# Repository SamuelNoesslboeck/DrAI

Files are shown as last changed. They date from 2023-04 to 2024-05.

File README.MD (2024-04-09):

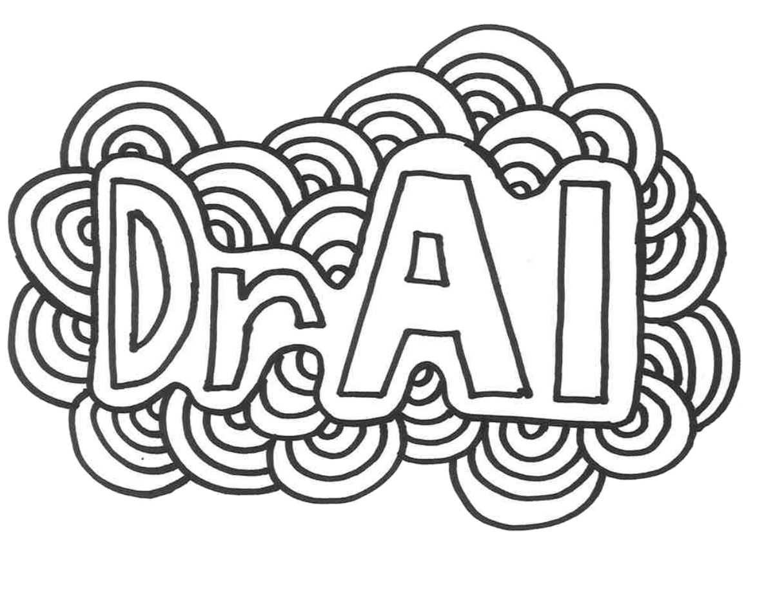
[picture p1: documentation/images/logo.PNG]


# DrAI

Diploma project estimated in January 2023 in collaboration with [**Ars Electronica Center Linz**](https://ars.electronica.art/) and the [higher secondary vocational college Neufelden](https://htl-neufelden.at).

## Thesis, repo folders and further reading

The thesis is available for everyone to read [here](/documentation/Projektbeschreibung.pdf).

All the important folders of this repository contains a *README.md*-file with basic information about the folder itself and important subfolders. As does this folder:

- [code](code/): Code projects for robot control, AI and more 
- [construction](construction/): Parts and drawings for the robot, electronics and other builds
- [documentation](documentation/): Images, graphics, the documentation and the written diploma thesis
- [drake_printer_files](https://github.com/sn-printer-files/drake_printer_files): A subrepository for managing all the *GCODE*-files for the 3D-printed parts of the project
- [electronics](electronics/): Contains all the schematics for the electronics of the project
- [sketches](sketches/): Sketches and basic concept art created for this project, indexed and documentated
- [standard](standard/): Folder with additional standard-parts, will be removed in the future

## Overview

- [DrAI](#drai)
  - [Thesis, repo folders and further reading](#thesis-repo-folders-and-further-reading)
  - [Overview](#overview)
  - [Summary](#summary)
    - [Goal](#goal)
    - [Task](#task)
      - [Software](#software)
      - [Robot](#robot)
  - [Construction](#construction)
  - [AI](#ai)
  - [Electronics](#electronics)

## Summary

### Goal

The goal of this project is to demonstrate the capabilities of AI in completing "creative" tasks in collaboration with humans.

### Task

The final result will be an interactive robot equipped with an AI trained to interpret pre-drawn sketches from the user and complete them with its own "creativity".  
To start this interaction, the user will have to draw some sketch onto a piece of paper, which then is transported into the robot. Once the sheet is in the robot, its goal is to unwrap its "creative" potentials by drawing additional lines onto the paper of the user. The opportunities are limitless here, the AI can for example create a forest next to a cottage the user has drawn onto the sheet, or a beach to some water and so on.

The project can be split up into the two main parts AI (or in general software) and the robot (hardware).

#### Software

First the software has to locate the sheet with a digital camera mounted to the tool and take a picture of it. Then all the lines drawn by the user are detected and interpreted. The fewer lines made by the user, the more "creative" the AI can be. All the merged lines generated are then transfered to the robot.

The software first puts the picture taken into a vision-transformer that creates a description for it, which is then used by a Stable Diffusion Algorithm to generate a colored RGB-image. Out of this images, another algorithm extracts the edges and merges them with the original image.

The robot os is made in rust and allows basic movements required to draw the lines. (See [sybot](https://github.com/SamuelNoesslboeck/sybot))

#### Robot

The robot has to, as already mentioned, be able to draw lines on an A5 sheet of paper. To do this, it will be equipped with a printer tool and three dynamic (X, Y, Z) axes that it can move to any exact position in range it desires.

The user interface should be as simple as possible, not more then two buttons even.

## [Construction](./construction/)

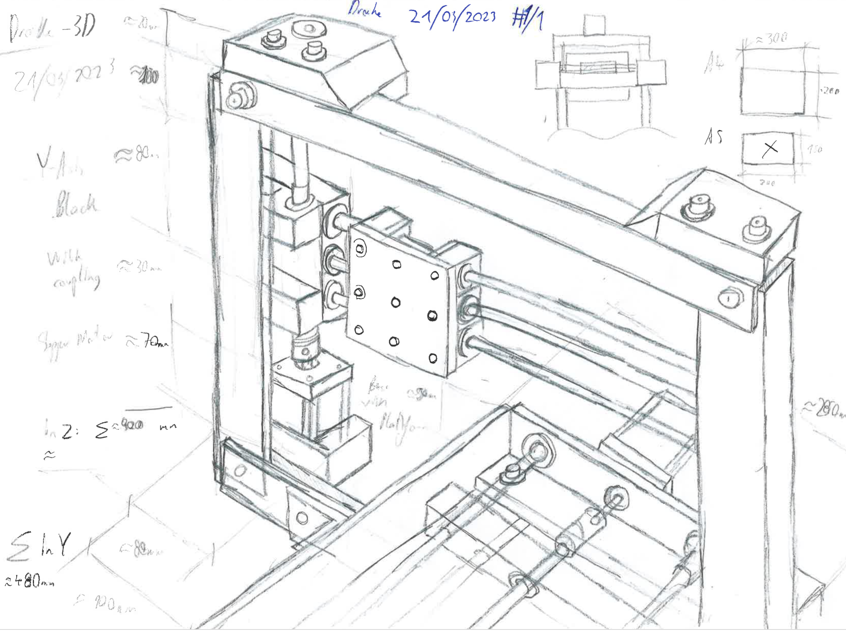
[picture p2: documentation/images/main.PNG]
Old sketch


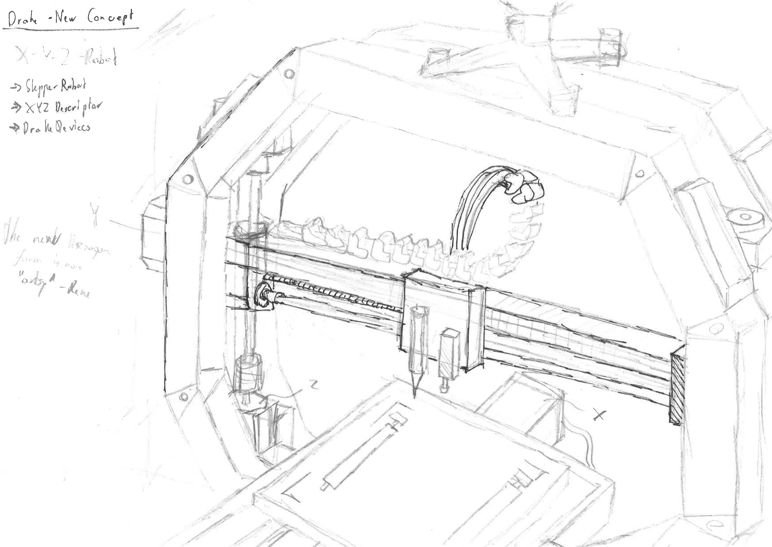
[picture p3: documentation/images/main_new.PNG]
New sketch


The construction is similar to the one of a 3D-Printer including three stepper-motor controlled linear axis, a BLTouch and endswitches to measure home position and more. A welded aluminum frame is the basis for the robot and with the vast majority of the other parts being 3D-printed, the manufactoring process turned out to be quite simple.

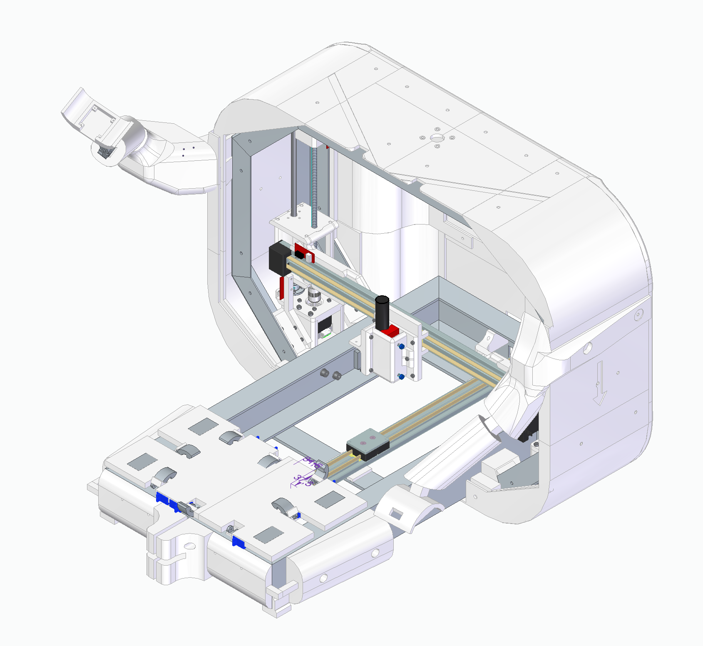
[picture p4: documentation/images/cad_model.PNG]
CAD


## AI

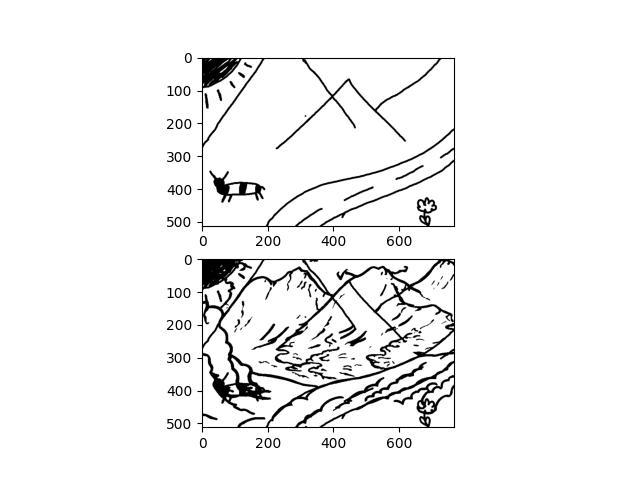
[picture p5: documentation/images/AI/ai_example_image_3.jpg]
AI Example 1


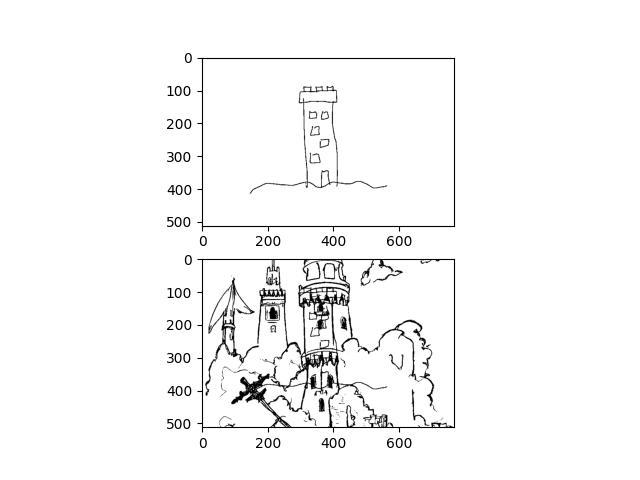
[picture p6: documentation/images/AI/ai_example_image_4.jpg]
AI Example 2


## Electronics

The electronics consist of the main robot driver and the additional control systems, with the main driver being equipped with multiple high-power stepper motor controllers, as we do not want the user to wait more than five minutes for their picture.

- [Driver README](./electronics/drake_electronics/README.md)

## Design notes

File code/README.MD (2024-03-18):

# Code

Contains all the code projects for robot control, AI and more

## Relevant subfolders

- [ai_pipeline](ai_pipeline/): Everything related to the AI-Pipeline
- [drake_ctrl](drake_ctrl/): The control software of the robot
- [network](network/): Helper scripts for the network connection
- [scripts](scripts/): Scripts and batch files required for setup, updating and maintaining
- [syact](https://github.com/SamuelNoesslboeck/syact): The *syact* library for stepper motor control and management of devices
- [sybot](https://github.com/SamuelNoesslboeck/sybot): The *sybot* library for robot controls
- [sylo](https://github.com/SamuelNoesslboeck/sylo): The *sylo* library for peripheral controls

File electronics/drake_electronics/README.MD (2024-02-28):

# drake electronics

## Summary

The main electronics of the drake robot, including four stepper controllers, a high amount of measurement devices, sensors and up to two cameras.

## Stepper controllers

Supplied with a high voltage and current of 24-36V and ~2A the motors need a powerful controller that can manage high step frequencies as microstepping is used. Assuming a step count of 200 with a microstepping of 16, the frequency required to create a speed of 10rev/s evaluates to 32kHz, which is about the maximum for stepper motor controllers of this size.

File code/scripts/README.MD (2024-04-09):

# Scripts

Scripts and batch files required for setup, updating and maintaining

## General scripts

General purpose scripts

- [env](env.sh)(.sh/.bat): Sets all the environment variables required for other scripts, executing in advance will not be required!
- [setup](setup.sh)(.sh/.bat): Setup script that should be called after installing to ensure functionality
- [update](update.sh)(.sh/.bat): Updates all repos if there are any available

## [Start scripts](./start/)

Scripts for starting up the main processes for a specific device (e.g. drai-camera).

- [camera.sh](start/camera.sh)
- [ctrl.sh](start/ctrl.sh)
- [server.sh](start/server.sh)
  
## Test scripts

Scripts for testing the functionallity of electronics and connections.

- []

### Standard test routine

To run the full [standard test routine](./testing.sh) run:

```sh
# Go to the project root directory, default being:
cd ~/DrAI

sh "code/scripts/testing.sh"
```

## Calibration scripts

Scripts for the calibration of the robot.

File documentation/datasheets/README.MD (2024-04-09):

# Datasheets

A list of datasheets for the components used in the project:

1. [PCA9685 Board](./1_pca9685_board.pdf): The servo driver board used in the drawing table
2. [PCA9685 Chip](./2_pca9685_chip.pdf): The servo driver chip

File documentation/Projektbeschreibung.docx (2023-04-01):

Projektbeschreibung

Ziel:

Ziel des Projektes ist es, die kreativen Möglichkeiten einer Künstlichen Intelligenz darzustellen.

Aufgabe:

Aufgabe des Projekts ist es, einen interaktiven Roboter mit einer künstlichen Intelligenz zu kombinieren. Die Aufgabe sollte hierbei sein, eine grobe vorgefertigte Skizze, fertig zu zeichnen im Sketch-Zeichen-Stil.

Hierfür zeichnet der Besucher zum Beispiel ein Haus aus einem Viereck und einem Dreieck auf ein A5 Papier. Dieses Blatt Papier wird nun auf eine Fläche des Roboters gelegt. Bei der Konstruktion des Roboters ist der dümmste anzunehmende Besucher, daB anzunehmen. Sobald das Blatt Papier am Roboter liegt, ist seine Aufgabe nun sich kreativ auszuleben. Er könnte zum Beispiel weitere Häuserskizzen zeichnen, um ein Dorf zu erstellen oder er könnte einen Wald neben dem Haus anfertigen. Die Möglichkeiten sind hierbei schier grenzenlos.

Dieses Projekt lässt sich in zwei Teile unterteilen. In den Roboter, der die Zeichnung auf das Blatt Papier bringt und die Software, die das anfänglich gezeichnete interpretiert und fertigstellt.

Software:

Ziel der Software ist es das Blatt Papier zu lokalisieren und eine digitale Version davon zu erstellen. Im nächsten Schritt werden die gezeichneten Linien erkannt. Aus den gesammelten Daten wird das Bild interpretiert und erweitert. Im letzten Schritt werden die zu zeichnenden Kanten an den Roboter weitergegeben. Um dies zu realisieren wird eine Kamera verwendet, die von der Vogelperspektive aus auf das Blatt Papier fotografiert. Diese digitale Version wird in einen V14-Transformer gegeben, dieser erzeugt eine Beschreibung der anfänglich gezeichneten Skizze. Aus der anfänglichen Skizze und den generierten Wörtern erzeugt ein Stable Diffusion Algorithmus ein färbiges RGB-Bild mit einer 512x512 Auflösung. Je nach einstellen der Parameter für den Diffusion Algorithmus werden die Bilder kreativer und haben mehr oder weniger mit dem am Anfang Gezeichneten zu tun. Aus dem neu erstellten Bild müssen nun die Kanten extrahiert werden, die charakteristisch für dieses Bild sind. Aus diesen Kanten und der Kamera Position sollten nun 2d-Coordinaten erzeugt werden die an den Roboter gesendet werden, damit dieser das Bild auf das Blatt Papier zeichnet.

Roboter:

Ziel des Roboters ist es ein A5 Blatt Papier unter die Kamera zu befördern. Sind die zu zeichnenden Daten empfangen, ist es die Aufgabe die Linien auf das Blatt Papier zu zeichnen. Wichtig ist hierbei mit dem dümmst anzunehmenden Benutzer zu rechnen. Dies hat zur Folge, dass der Roboter so konstruiert werden sollte, dass er wenig beschädigt werden kann und wenn etwas beschädigt ist, es einfach ist dies auszutauschen. Auch ist es wichtig, dass sich der Besucher nicht weh tun kann. Dies könnte passieren in dem der Besucher zum Beispiel seinen Finger in einen Mechanismus hineinsteckt und dieser den Besucher Schmerzen zufügt.

Um diese Aufgabe zu erfüllen, wird ein 3D-Drucker ähnlicher Roboter gebaut. Durch diese Konstruktion ist es möglich mit einem Stift in 3-Achsen zu verfahren. X-Y-Achse um einen Punkt anzufahren und Z-Achse um den Stift zu heben und zu senken. Die Außenmaße der Maschine bewegen sich im Bereich 700x480x400 mm. Die Ansteuerung der Motoren erfolgt mithilfe einer von Herrn Nösselböck angefertigten Software, die eine hohe Punktsteuerung ermöglicht. Diese hohe Punktsteuerung wird des Weiteren mechanisch mit Stepper Motoren ermöglicht. Preislich werden die Kosten des Roboters 2000€ betragen.

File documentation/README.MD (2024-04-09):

# Documentation

Descriptions, schematics, general documentation and even the diploma thesis itself can be read here.

- [Diploma thesis](./Projektbeschreibung.pdf): The diploma thesis as it was published in German, including summaries of setup instructions, details and more

## Relevant content

- [Setup](./setup.md): Information about setting up the project
- [Update](./updating.md): How to correctly update the software
- [Testing](./testing.md): Testing components and checking functionality

## Other content

- [competitions](./competitions/): Information about all the competitions entered with this project
- [datasheets](./datasheets/): List of datasheets for the components used in the project

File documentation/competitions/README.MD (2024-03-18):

# Competitions

An overview of all the competitions entered with this project and corresponding results.

## Overview

- [ ] [ARS Prix U19](./ARS%20PRIX%20U19/)
  - Enter till 02/04/2024
- [ ] [Autstanding](./Autstanding/)
  - Enter till 15/04/2024
- [ ] [BOSCH Innovations](./BOSCH%20Innovations/)
  - Enter till 11/04/2024
- [ ] [FH Salzburg Matura Award](./FH%20Salzburg%20Matura%20Award/)
 - Enter till 24/05/2024
- [ ] [JK Engineering Foerderpreis](./JK%20Engineering%20Foerderpreis/)
  - Enter till 31/05/2024
- [x] [Jugend Innovativ](./Jugend%20Innovativ/)
  - Entry done! Waiting for results
- [ ] [TÜV AUSTRIA Wirtschaftspreis](./TUEV%20AUSTRIA%20Wirtschaftspreis/)
  - Enter till 31/06/2024

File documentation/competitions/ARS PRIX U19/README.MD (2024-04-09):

# [ARS PRIX U19](https://calls.ars.electronica.art/2024/u19/project/edit/9909/)

Status: *Project created*

Deadline: 

## TODO

- [x] Create Project
- [ ] Fill out project information
  - [x] Lebenslauf Samuel
  - [ ] Lebenslauf Rene
- [ ] Upload project images/details etc. (Till March 1)

## Descriptions

### Kurzbeschreibung der Arbeit

Ziel dieses Projekts ist es, die Fähigkeiten von KI bei der Erledigung "kreativer" Aufgaben in Zusammenarbeit mit Menschen zu demonstrieren und menschliche Kreativität nachzuahnen. Der Roboter ist außerdem als Teil von Workshops oder sogar der Ausstellung des ARS Electronica Centers geplant.

Das Endergebnis ist ein interaktiver Roboter sein, der mit einer KI ausgestattet ist, die darauf trainiert ist, vorgezeichnete Skizzen des Benutzers zu interpretieren und sie mit ihrer eigenen "Kreativität" zu vervollständigen. Sobald sich das Blatt im Roboter befindet, ist es sein Ziel, sein Potenzial zu entfalten, indem er zusätzliche Linien auf das Papier des Benutzers zeichnet. Die Möglichkeiten sind hier grenzenlos, die KI kann z. B. einen Wald neben einem Häuschen erschaffen, oder einen Strand neben ein Meer und so weiter.

### Technische Details der Arbeit

Das Projekt beinhaltet ein komplexes Netz aus verschiedensten Algorithmen geschrieben in Python und der eher neuen Systemsprache Rust.

Zuerst wird die exakte Platzierung des Papiers mit der Skizze mithilfe von einer Verschachtelung verschiedener Bildanalysemethoden, wie Canny-Edge-Detection, Harris-Corner-Detection usw., überprüft. So kann der Roboter trotz Ungenauigkeiten des Users beim Einführen des Papiers korrekt zeichnen. 
Die gezeichnete Skizze wird dann durch einen Clip-Interogator in einen Text-Prompt übertragen. Nun wird ein Large Language Model benutzt um der Zeichnung etwas hinzuzufügen. Hierbei ist Prompt Engeneering von nöten um den Output zu verbessern. Würden wir den neu generierten Prompt und das Originalbild durch eine Stable Diffusion Img2Img Pipeline laufen lassen würde zu wenig Kreativität im neuen Bild entstehen, da der Diffusion Algorithmus mit niedriger Strength keine neuen Ansätze generiert und mit zu hoher Strength das Originalbild verschwindet und etwas Unbrauchbares entsteht. Um dieses Problem zu umgehen werden zufällige Linien in das Originalbild gezeichnet. Durch diese simple Methode mit der Kombination der verschiedenen neuronalen Netzwerke und der restlichen komplexen Algorithmen, ist es möglich den Stable Diffusion Algorithmus Kreativität zu verleihen. Da der gesamte Algorithmus sehr leistungsaufwändig ist wurde das ganze Projekt auf die CPU / RAM und GPU / V-RAM diversifiziert und ausgelagert um optimale Leistung auf kostengünstiger Hardware zu ermöglichen.

Eine weiterer Aspekt ist die Steuerung des Roboters, die zu großen Teilen von uns in Rust angefertigt wurde, da es etwas vergleichbares in dieser Sprache noch nicht gibt. Rust hat uns durch ihre Eleganz, Sicherheit und überragende Performance überzeugt. Durch sie ist es möglich, die komplette Steuerung inklusive Bahnberechnungen auf einem simplen Raspberry Pi Einplatinencomputer laufen zu lassen. Da in einem Museum die Aufmerksamkeitsspanne der Besucher eher kurz ist, muss schnell gezeichnet werden. Was durch die robuste Konstruktion, die leistungsstarke Elektronik und die Software, die hochwertige Anlaufkurven für die Motoren berechnet, gewährleistet wird. 

### Projektgeschichte

Eine Internetrecherche in Zusammenarbeit mit dem Projektleiter ergab, dass es zwar schon Zeichenroboter gab, die auf gewisse Datensätze trainiert wurden, jedoch funktionierten diese nur auf kleine Datensätze oder Zeichnungen und wiesen nicht die benötigte gewünschte Vielfältigkeit und Kreativität auf. Auch waren viele der existierenden Konzepte nicht für den Museumsbetrieb geeignet.
Die anfängliche Idee des Projektes war, zu einer bestehenden Zeichnung etwas Kreatives hinzuzufügen und die Besucher*innen mit der KI kollaborieren zu lassen. Das Projekt sollte zur Demonstration von kreativer Zusammenarbeit von Künstlicher Intelligenz und Mensch dienen. 
Zu Beginn des Projektes existierte die Meinung, künstliche Intelligenz werde in den nächsten Jahren zu einem neuen Werkzeug für die Menschheit, wie die Erfindung des Taschenrechners. Bereits zu dieser Zeit existierten diverse Algorithmen, mit denen sich durch menschliches Einwirken Herausragendes entwickeln lässt. Durch Programme wie Github Copilot lassen sich komplexe Programme in beliebigen Programmiersprachen durch eine Textbeschreibung entwickeln. Oft genügt eine einfache Beschreibung des Lösungsansatzes und schon liefert ein Large Language Model (LLM) wie GPT-4 den Programmcode. Was jedoch hierbei wichtig ist, ist die Beschreibung des Lösungsansatzes. Neuronale Netzwerke sind nur so gut wie ihre Trainingsdaten. Befindet sich das Problem nicht in den Datensätzen, so fällt es dem Programm meist schwer, eine komplexe Lösung zu finden, die auch wirklich funktioniert. Hierbei wird die menschliche Kreativität benötigt, um einen Lösungsansatz zu finden, der dann beschrieben und in Code umgesetzt wird. 
Mit Bildern ist es das gleiche, es wird menschliche Kreativität benötigt, um kreative Textbeschreibungen für Bilder zu finden, die im Anschluss gezeichnet werden. Je weiter die Forschung des Algorithmus fortschritt, desto mehr festigte sich die Erkenntnis, dass diese These inkorrekt ist. Der Programmcode hat einerseits die Möglichkeit, aus Bestehendem etwas Neues zu erzeugen und andererseits aus einem weißen Blatt Papier ohne textliche Beschreibungen oder menschliches Einwirken kreative Bilder zu malen. Es ist eine philosophische Frage, ob Maschinen kreativ sein können oder nicht, jedoch sehen die Resultate sehr vielversprechend aus. Die Frage, ob KI kreativ sein kann, wird eher zur Frage, wann KI kreativer wird, als die Menschheit es derzeit ist.
Der zunächst beschriebene Algorithmus versucht die menschliche Kreativität nachzuahmen, indem er generative Künstliche Intelligenz mit zufällig in das Eingangsbild generierten Inhalten kombiniert. Die Innovation liegt in dieser Interpretation menschlicher Kreativität als genau dieser Kombination von zufälligen Impulsen in der menschlichen Wahrnehmung, abgebildet durch die Zufallsgeneratoren, und der Erkennung von Mustern, abgebildet durch KI.

### Kurzbiographie Samuel

Schon lange bastelt Samuel Nösslböck an den verschiedensten Projekten im Bereich der Robotik. Dabei glaubt er an die Relevanz der Kunst und Kreativität in der sonst sehr regulierten und genormten Technik. 

So entstand 2022 SyLa, eine für Netzwerkanwendungen optimierte Skriptsprache, 
Im Jahre 2023 SyArm, ein Roboterarm gebaut aus simplen Teilen und im Jahr darauf in Kooperation mit Rene Schwarz DrAI, ein intelligenter Zeichenroboter mit neuen Ansätzen zur Interpretation und Nachahmung von Kreativität.

### Kurzbiographie Rene

Rene Schwarz war von klein auf sehr technikbegeistert. Schon lange kannte er Samuel Nösslböck, welcher ihn überredete, die Programmiersprache Python zu lernen. Die Faszination für den Marvel-Charakter Ironman und dessen interaktives Sprachprogramm Jarvis, setzen den ersten Grundstein für die Begeisterung für KI.

Mit 15 Jahren entdeckte er Deep Learning. 3 Jahre später folgte die erste Gesichteserkennungs- und Identifikationssoftware Facevec. Im Jahre 2023 entwickelte er eine Rechenleistungsoptimierte Speech to Text Software und im Jahr darauf in Kooperation mit Samuel Nösslböck DrAI, ein intelligenter Zeichenroboter mit neuen Ansätzen zur Interpretation und Nachahmung von Kreativität.

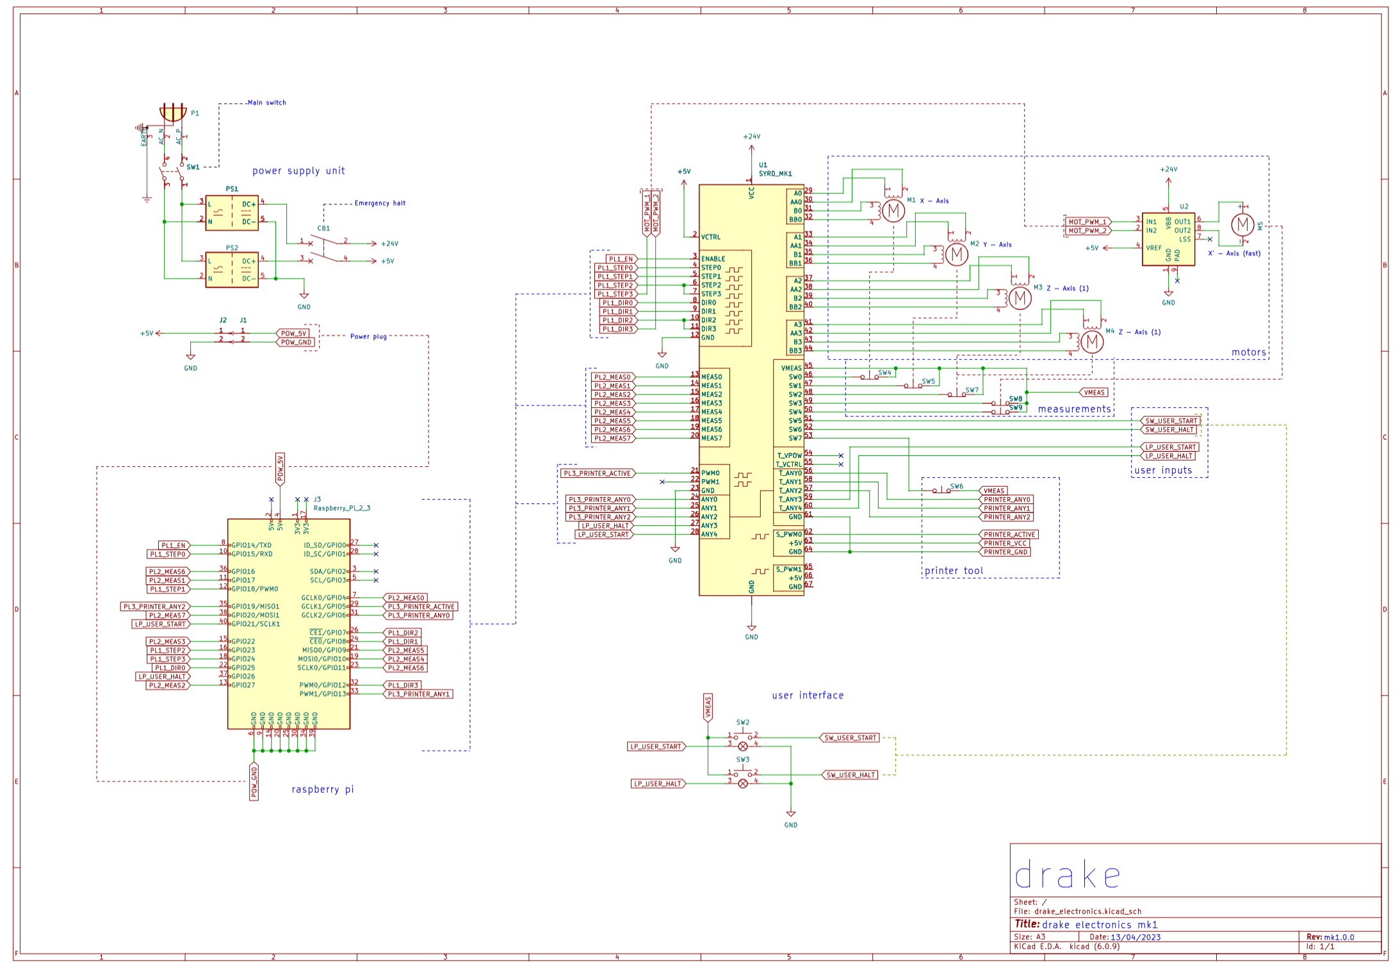
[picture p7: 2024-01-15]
documentation/images/electronics_main.PNG

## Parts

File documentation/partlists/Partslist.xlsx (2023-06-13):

Electronics
ID | Circuit | General | Name | Link | Quan. | Single | Total |  | Status
1 | J3 | E_C1 | Raspberry PI Zero |  | 1 | €60.00 | €60.00 |  | Unavailable
2 |  | E_C2 | Arduino Uno | https://store.arduino.cc/products/arduino-uno-rev3 | 1 | €25.00 | €25.00 |  | Ordered
3 | U1_M1-4 | E_M1-4 | Nema 17 Stepper Motor | https://www.omc-stepperonline.com/e-series-nema-17-bipolar-55ncm-77-88oz-in-2a-42x48mm-4-wires-w-1m-cable-connector-17he19-2004s | 4 | €10.00 | €40.00 |  | Part. Available
4 | U1_M5-6 | E_M5-6 | MG996R Servo Motor | https://www.amazon.com/Hosyond-MG996R-Digital-Motors-Helicopter/dp/B0BYDJF3RC | 2 | €6.00 | €12.00 |  | Available
5 | M5 | E_M7 | DC Motor |  | 1 | €35.00 | €35.00
6 | PS1 | E_PS1 | Power Supply 36V | https://www.omc-stepperonline.com/350w-36v-9-7a-115-230v-switching-power-supply-stepper-motor-cnc-router-kits-s-350-36 | 1 | €30.00 | €30.00
7 | U2 | E_U1 | DC Motor controller |  | 1 | €10.00 | €10.00
8 | SW1 | E_SW1 | Main switch (AC) |  | 1 | €10.00 | €10.00
9 | SW2-3 | E_SW2-3 | Push buttons |  | 2 | €5.00 | €10.00
10 | SW4-5,7,8 | E_SW4-7 | Endswitches |  | 4 | €0.50 | €2.00
11 | SW6 | E_SW8 | Measurement sensor (exact) |  | 1 | €15.00 | €15.00
12 |  |  | Misc. Connectors |  | 1 | €50.00 | €50.00
13 |  |  | Misc. Cables |  | 1 | €30.00 | €30.00
14 |  |  | Misc. Cable management |  | 1 | €80.00 | €80.00
15 |  |  |  |  |  |  | €0.00
 |  |  |  |  |  |  | €0.00
Total |  |  |  |  |  |  | €409.00
 |  |  |  |  |  |  | 1.2 | Safety factor
 |  |  |  |  |  | Total | €490.80

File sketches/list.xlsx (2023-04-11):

ID | Name | Format | Date
1 | robot_general | A4 x 2 | 2023-03-21
2 | connector | A4 x 1 | 2023-03-14

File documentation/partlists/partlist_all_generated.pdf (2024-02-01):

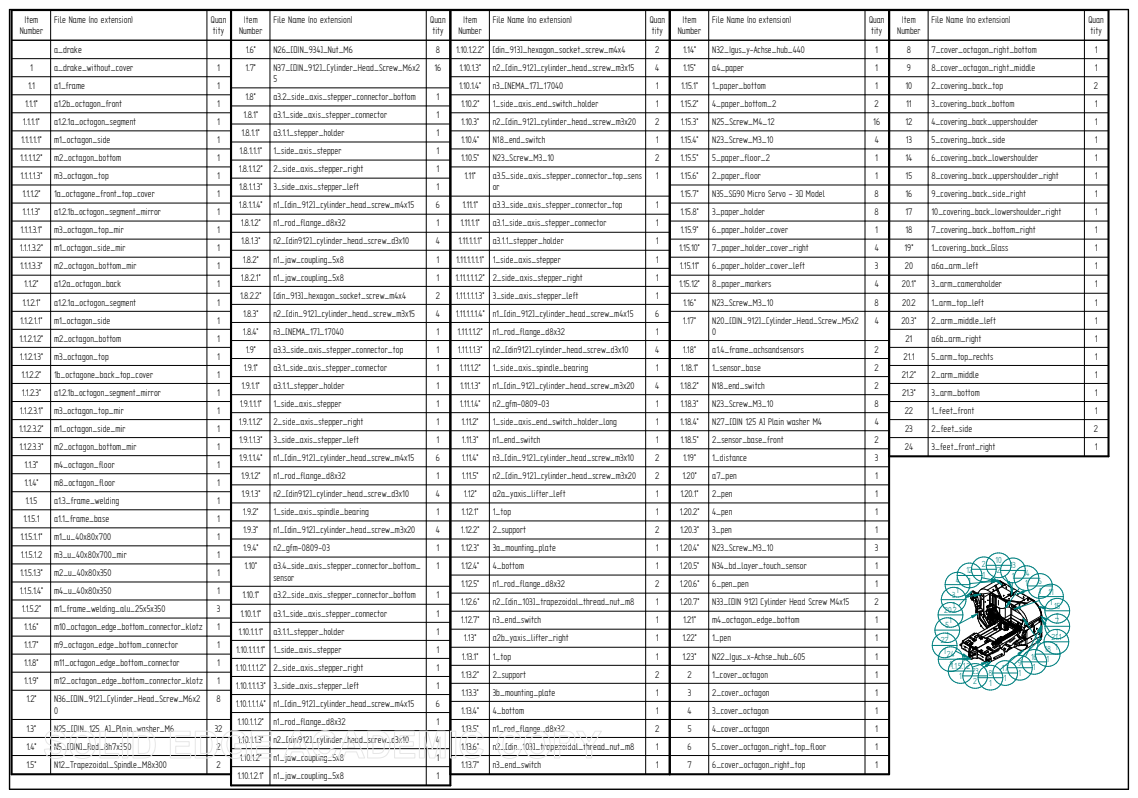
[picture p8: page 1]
N12_Trapezoidal_Spindle_M8x300; n3_end_switch; 6_cover_octagon_right_top

Item Number | File Name (no extension) | Quan tity | Item Number | File Name (no extension) | Quan tity | Item Number | File Name (no extension) | Quan tity | Item Number | File Name (no extension) | Quan tity | Item Number | File Name (no extension) | Quan tity

a_drake | | 1.6* | N26_[DIN_934]_Nut_M6 | 8 | 1.10.1.2.2* | [din_913]_hexagon_socket_screw_m4x4 | 2 | 1.14* | N32_Igus_y-Achse_hub_440 | 1 | 8 | 7_cover_octagon_right_bottom | 1
1 | a_drake_without_cover | 1 | 1.7* | N37_[DIN_912]_Cylinder_Head_Screw_M6x2 5 | 16 | 1.10.1.3* | n2_[din_912]_cylinder_head_screw_m3x15 | 4 | 1.15* | a4_paper | 1 | 9 | 8_cover_octagon_right_middle | 1
1.1 | a1_frame | 1 | | | | 1.10.1.4* | n3_[NEMA_17]_17040 | 1 | 1.15.1* | 1_paper_bottom | 1 | 10 | 2_covering_back_top | 2
1.1.1* | a1.2b_octagon_front | 1 | | | | 1.10.2* | 1_side_axis_end_switch_holder | 1 | 1.15.2* | 4_paper_bottom_2 | 2 | 11 | 3_covering_back_bottom | 1
1.1.1.1* | a1.2.1a_octogon_segment | 1 | | | | 1.10.3* | n2_[din_912]_cylinder_head_screw_m3x20 | 2 | 1.15.3* | N25_Screw_M4_12 | 16 | 12 | 4_covering_back_uppershoulder | 1
1.1.1.1.1* | m1_octagon_side | 1 | | | | 1.10.4* | N18_end_switch | 1 | 1.15.4* | N23_Screw_M3_10 | 4 | 13 | 5_covering_back_side | 1
1.1.1.1.2* | m2_octagon_bottom | 1 | | | | 1.10.5* | N23_Screw_M3_10 | 2 | 1.15.5* | 5_paper_floor_2 | 1 | 14 | 6_covering_back_lowershoulder | 1
1.1.1.1.3* | m3_octagon_top | 1 | | | | 1.11* | a3.5_side_axis_stepper_connector_top_sens or | 1 | 1.15.6* | 2_paper_floor | 1 | 15 | 8_covering_back_uppershoulder_right | 1
1.1.1.2* | 1a_octagone_front_top_cover | 1 | | | | | | | 1.15.7* | N35_SG90 Micro Servo - 3D Model | 8 | 16 | 9_covering_back_side_right | 1
1.1.1.3* | a1.2.1b_octogon_segment_mirror | 1 | | | | | | | 1.15.8* | 3_paper_holder | 8 | 17 | 10_covering_back_lowershoulder_right | 1
1.1.1.3.1* | m3_octagon_top_mir | 1 | | | | | | | 1.15.9* | 6_paper_holder_cover | 1 | 18 | 7_covering_back_bottom_right | 1
1.1.1.3.2* | m1_octagon_side_mir | 1 | | | | | | | 1.15.10* | 7_paper_holder_cover_right | 4 | 19* | 1_covering_back_Glass | 1
1.1.1.3.3* | m2_octagon_bottom_mir | 1 | | | | | | | 1.15.11* | 6_paper_holder_cover_left | 3 | 20 | a6a_arm_left | 1
1.1.2* | a1.2a_octagon_back | 1 | | | | | | | 1.15.12* | 8_paper_markers | 4 | 20.1* | 3_arm_cameraholder | 1
1.1.2.1* | a1.2.1a_octogon_segment | 1 | | | | | | | 1.16* | N23_Screw_M3_10 | 8 | 20.2 | 1_arm_top_left | 1
1.1.2.1.1* | m1_octagon_side | 1 | | | | | | | 1.17* | N20_[DIN_912]_Cylinder_Head_Screw_M5x2 0 | 4 | 20.3* | 2_arm_middle_left | 1
1.1.2.1.2* | m2_octagon_bottom | 1 | | | | | | | | | | 21 | a6b_arm_right | 1
1.1.2.1.3* | m3_octagon_top | 1 | | | | | | | | | | 21.1 | 5_arm_top_rechts | 1
1.1.2.2* | 1b_octagone_back_top_cover | 1 | | | | | | | | | | 21.2* | 2_arm_middle | 1
1.1.2.3* | a1.2.1b_octogon_segment_mirror | 1 | | | | | | | | | | 21.3* | 3_arm_bottom | 1
1.1.2.3.1* | m3_octagon_top_mir | 1 | | | | | | | | | | 22 | 1_feet_front | 1
1.1.2.3.2* | m1_octagon_side_mir | 1 | | | | | | | | | | 23 | 2_feet_side | 2
1.1.2.3.3* | m2_octagon_bottom_mir | 1 | | | | | | | | | | 24 | 3_feet_front_right | 1
1.1.3* | m4_octagon_floor | 1 | | | | | | | | | | 10 2 13 12 1
1.1.4* | m8_octagon_floor | 1
1.1.5 | a1.3_frame_welding | 1
1.1.5.1 | a1.1_frame_base | 1
1.1.5.1.1* | m1_u_40x80x700 | 1
1.1.5.1.2 | m3_u_40x80x700_mir | 1
1.1.5.1.3* | m2_u_40x80x350 | 1 | | | | | | | | | | 2
1.1.5.1.4* | m4_u_40x80x350 | 1
1.1.5.2* | m1_frame_welding_alu_25x5x350 | 3
1.1.6* | m10_octagon_edge_bottom_connector_klotz | 1
1.1.7* | m9_octagon_edge_bottom_connector | 1
1.1.8* | m11_octagon_edge_bottom_connector | 1
1.1.9* | m12_octagon_edge_bottom_connector_klotz | 1
1.2* | N36_[DIN_912]_Cylinder_Head_Screw_M6x2 0 | 8

1.8* | a3.2_side_axis_stepper_connector_bottom | 1
1.8.1* | a3.1_side_axis_stepper_connector | 1
1.8.1.1* | a3.1.1_stepper_holder | 1
1.8.1.1.1* | 1_side_axis_stepper | 1
1.8.1.1.2* | 2_side_axis_stepper_right | 1
1.8.1.1.3* | 3_side_axis_stepper_left | 1
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

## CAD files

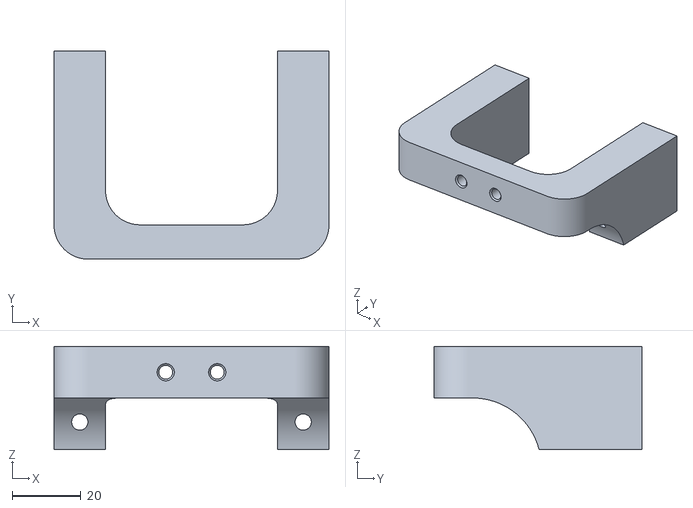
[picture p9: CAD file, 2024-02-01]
construction/a1_frame/a1.a3_sensors/stl/1_sensor_base.stl
80.0 x 60.6 x 30.0

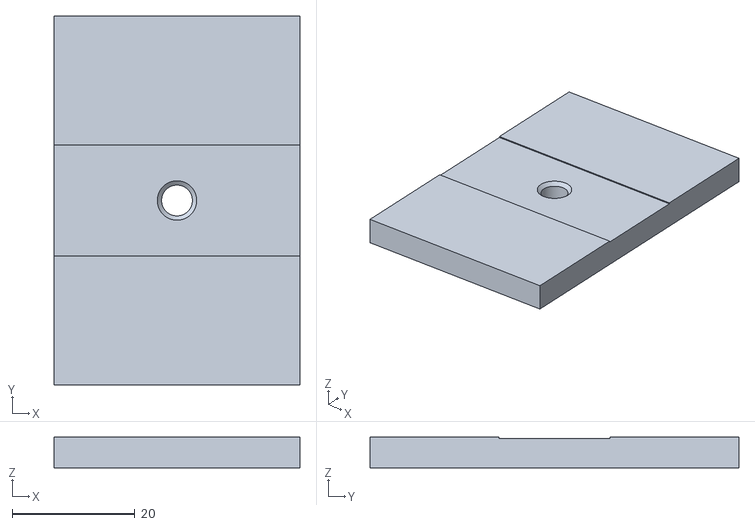
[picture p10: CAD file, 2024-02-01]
construction/a1_frame/stl/1_distance.stl
40.0 x 60.0 x 5.00

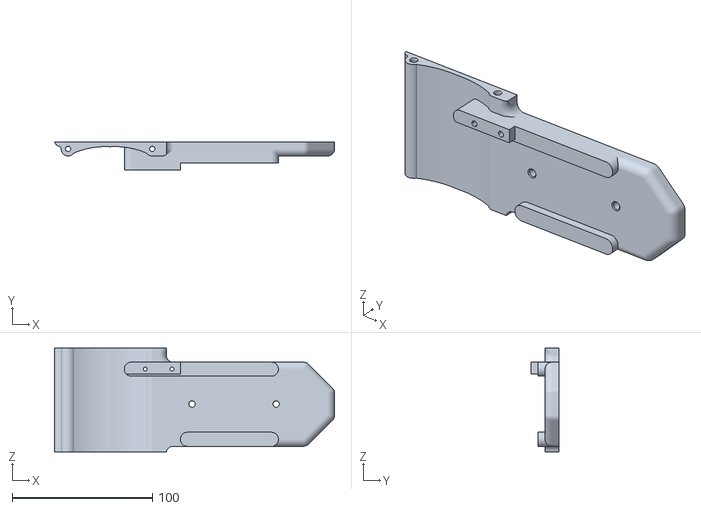
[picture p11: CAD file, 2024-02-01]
construction/a2_yaxis/stl/3a_mounting_plate.stl
199.8 x 20.0 x 74.0

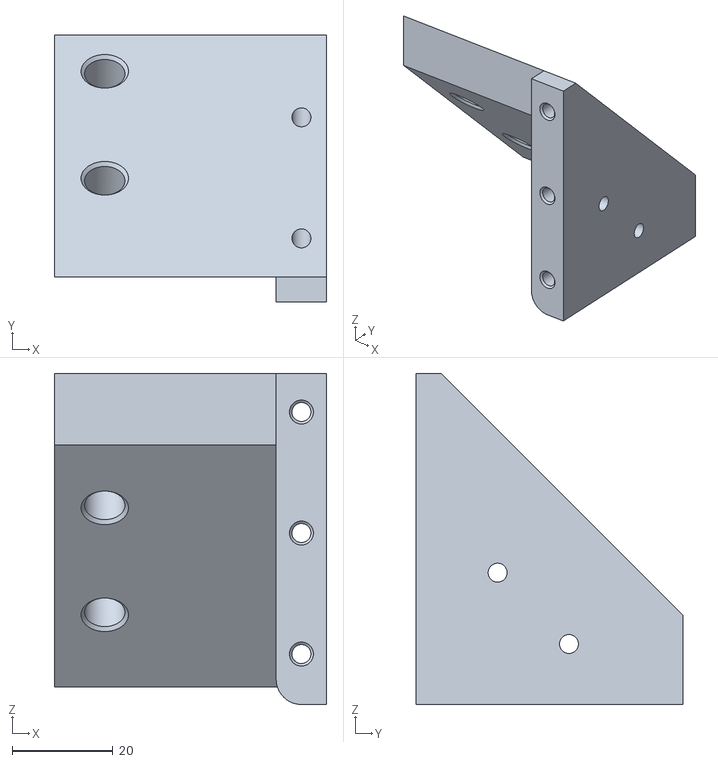
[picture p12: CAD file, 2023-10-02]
construction/a3_sideaxis/a3.a1_sideaxis_stepper_connector/a3.a1.a1_stepper_mount/stl/3_connector_side_b.stl
54.0 x 53.0 x 65.6

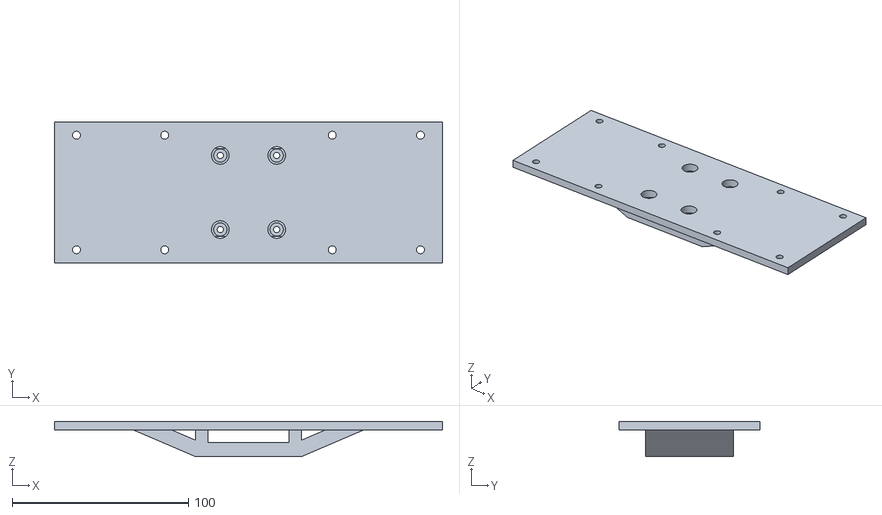
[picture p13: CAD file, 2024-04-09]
construction/a4_drawing_table/stl/1_bottom_connector.stl
220.0 x 80.0 x 20.0

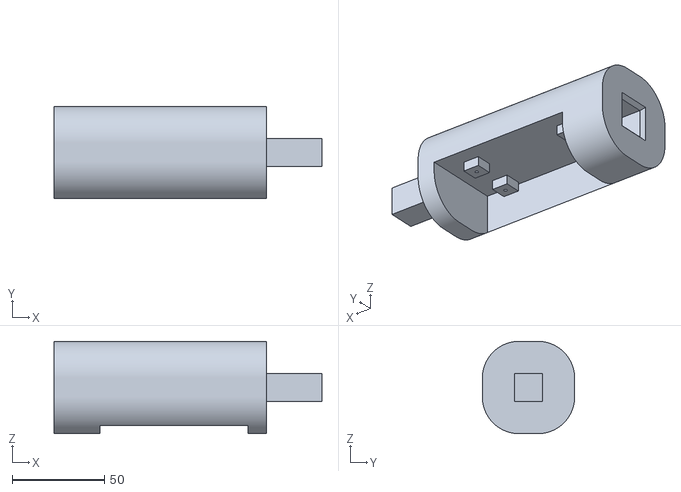
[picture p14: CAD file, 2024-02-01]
construction/a6_arm/a6.a1_arm_left/stl/2_middle_segment.stl
145.0 x 50.0 x 50.0

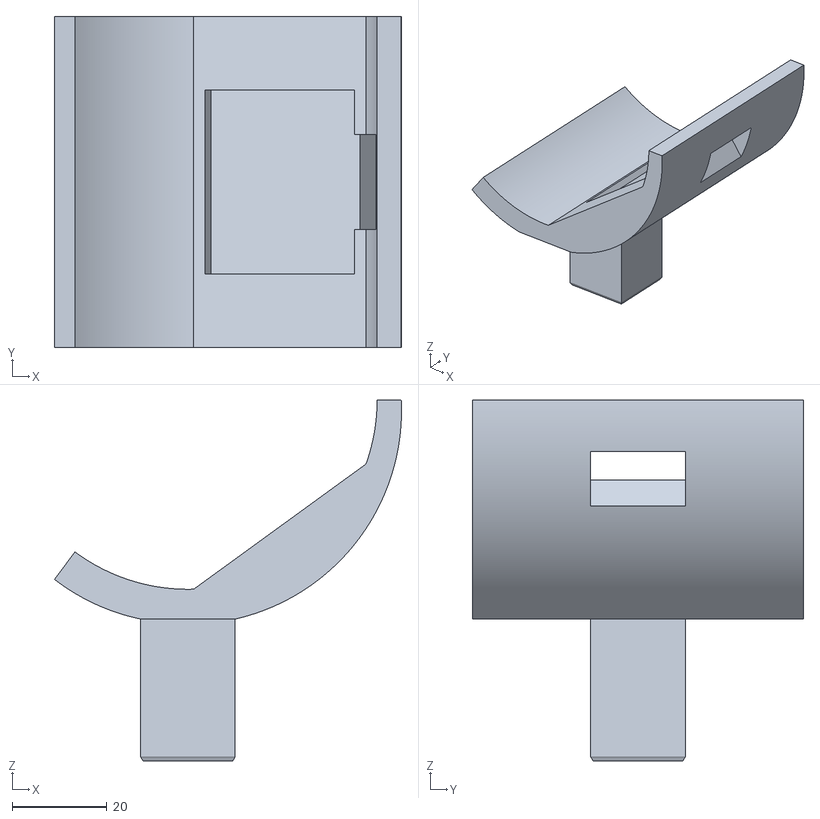
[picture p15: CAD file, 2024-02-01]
construction/a6_arm/a6.a2_arm_right/stl/3_bottom_segment.stl
73.4 x 70.0 x 76.3

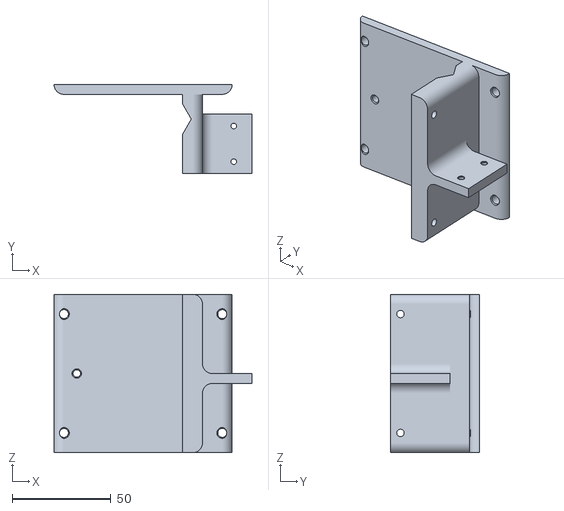
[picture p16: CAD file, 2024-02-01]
construction/a7_pen_mount/stl/2_body.stl
100.0 x 45.0 x 80.0

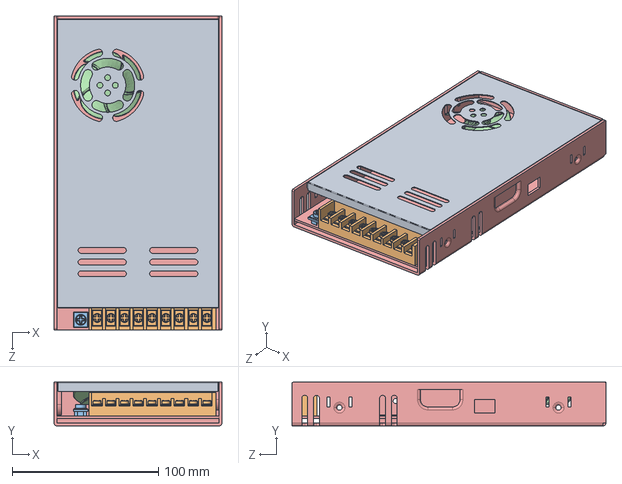
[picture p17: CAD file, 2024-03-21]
construction/a9_trunk/electronics/e2_lrs-350-24.step
115.0 x 30.0 x 215.0 mm

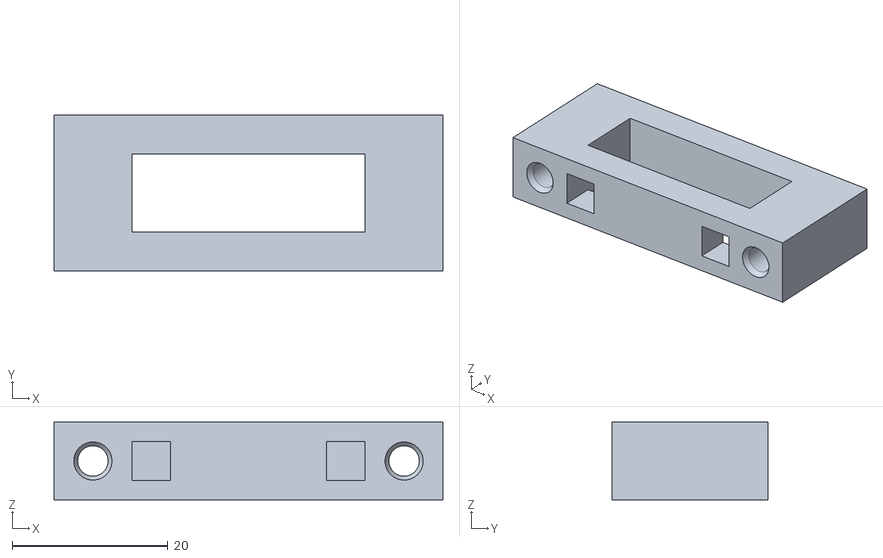
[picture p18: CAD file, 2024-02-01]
construction/c2_cover_octagon/stl/c2.5_cover_octagon_cable_holder.stl
50.0 x 20.0 x 10.0

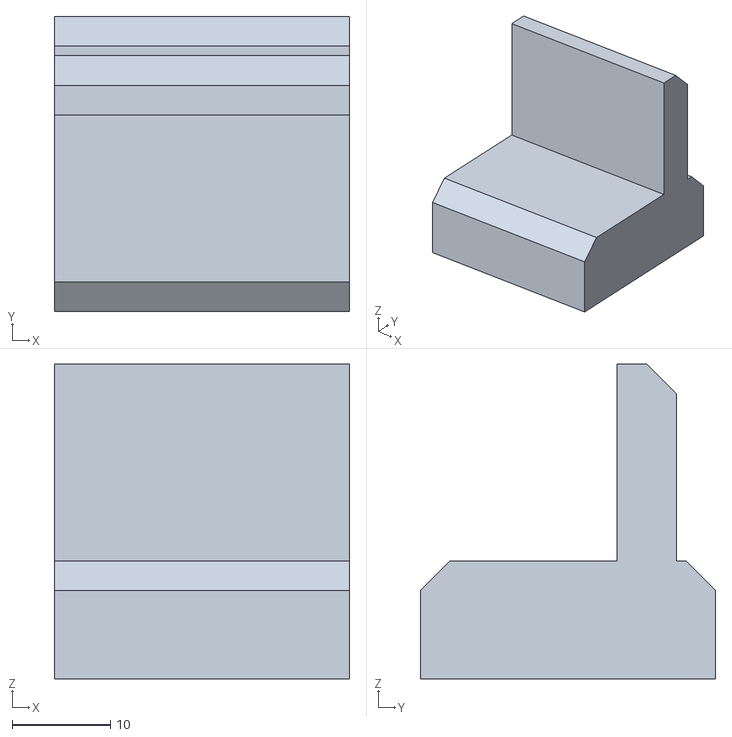
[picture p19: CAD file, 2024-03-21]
construction/m_misc/stl/1_foot.stl
30.0 x 30.0 x 32.0

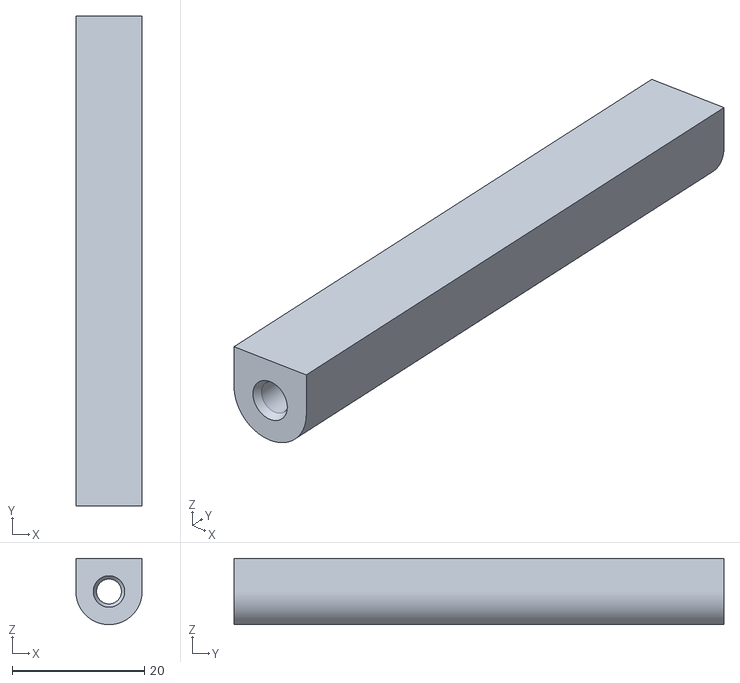
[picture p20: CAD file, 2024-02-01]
construction/a2_yaxis/stl/2_support.stl
10.0 x 74.0 x 10.00

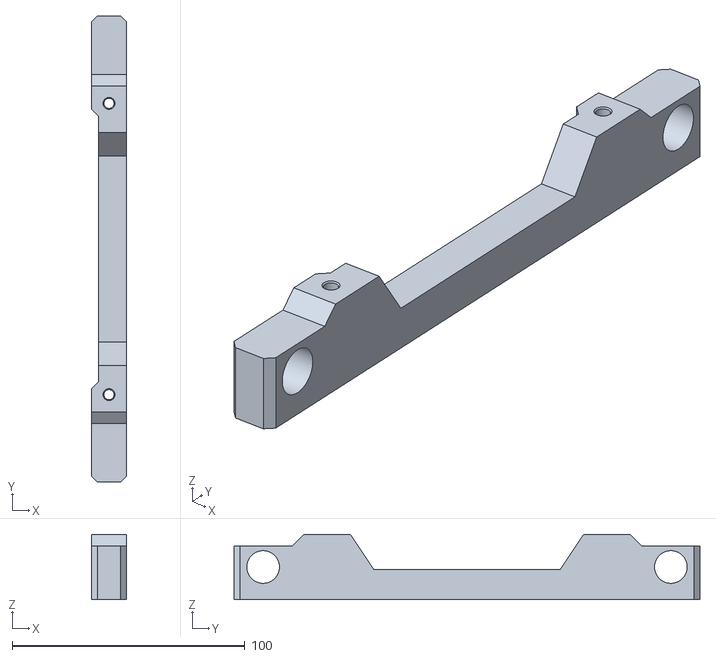
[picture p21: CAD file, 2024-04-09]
construction/a4_drawing_table/stl/10_roll_connector.stl
15.0 x 200.0 x 28.0

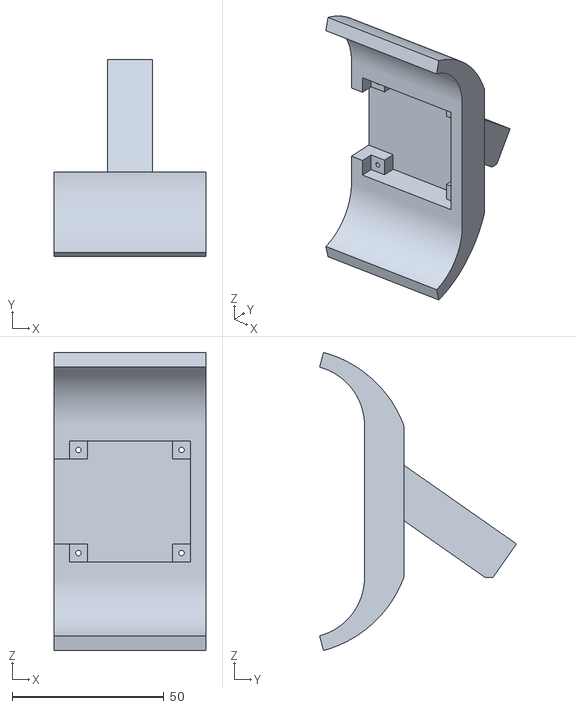
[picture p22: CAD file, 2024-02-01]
construction/a6_arm/a6.a1_arm_left/stl/3_bottom_segment.stl
50.0 x 64.9 x 98.3

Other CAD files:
construction/a3_sideaxis/a3.a1_sideaxis_stepper_connector/a3.a1.a1_stepper_mount/stl/2_connector_side_a.stl
construction/a6_arm/a6.a2_arm_right/stl/2_middle_segment.stl
construction/a7_pen_mount/stl/4_cheek.stl
construction/a9_trunk/electronics/e1_dm422t.step
construction/a1_frame/a1.a2_frame_octagon/1b_octagon_back_top_cover.psm
construction/a1_frame/a1.a2_frame_octagon/1f_octagon_front_top_cover.psm
construction/a1_frame/a1.a2_frame_octagon/a1.a2.a1a_octagon_segment/modified/m1_octagon_side.psm
construction/a1_frame/a1.a2_frame_octagon/a1.a2.a1a_octagon_segment/modified/m2_octagon_bottom.psm
construction/a1_frame/a1.a2_frame_octagon/a1.a2.a1a_octagon_segment/modified/m3_octagon_top.psm
construction/a1_frame/a1.a2_frame_octagon/a1.a2.a1b_octagon_segment_mirror/modified/m1_octagon_side_mir.psm
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

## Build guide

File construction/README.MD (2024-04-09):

# Construction

The construction is split up in many subassemblies and groups, which are featured and explained below.

## General information

### Naming system

In order to keep the project clean, the filesystem for the construction has a strict naming scheme. 

- Assemblies are referenced with an "a" prefix. Depending on the type of assembly a number can be added:
  - The main assembly has no number (e.g. "a_drake")
  - Subassemblies have a number attached to them (e.g. "a1_frame")
  - There can be subassemblies of subassemblies (e.g. "a1.1_frame_base")
- Standard parts have an "n{part-number}_" prefix
  - They are placed in a "standard" directory
- Modified parts (standard parts with modifications) have an "m{part-number}_" prefix
  - They are placed in a "modified" directory
- Custom parts just have their part number as prefix "{part-number}_"
  - They are placed into the assembies root

### Orientation

## Subassemblies

The important rule about subassemblies is, that they should always work on their own. This can of course mean that standard parts can be found multiple times in a construction.
The user interface has been kept as simple as possible, a button to start the process and an emergency-halt in case something goes wrong.

- [[A1] Frame](./a1_frame/): Base aluminium frame
- [[A2] Y-Axis](./a2_yaxis/): Y-Axis without the drawing head
- [[A3] Sideaxis](./a3_sideaxis/): Sideaxes used to move the `Y-Axis` in Z direction
- [[A4] Drawing Table](./a4_paper/): Drawing table with servos and clamps
- [[A5] Head](./a5_head/): A simple head used to track the user while drawing for more interaction
- [[A6] Arm](./a6_arm/): Both arms, one equipped with a camera
- [[A7] Pen mount](./a7_pen_mount/): Drawing head with pen mount
- [[A8] User terminal](./a8_user_terminal/): User terminal with buttons to interact with the machine
- [[A9] Trunk](./a9_trunk/): Trunk with the electronics inside

## Groups

- [[C1] Front cover](./c1_cover_front/): Cover parts used in the front
- [[C2] Octagon cover](./c2_cover_octagon/): Cover parts placed around the octagon

## [Misc](./m_misc/)

Remaining parts that do not fit in a group or subassembly

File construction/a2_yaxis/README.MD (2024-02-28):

# Y-Axis

## 3D-Printing

### 1_top

- Accuracy: medium
- Stability: high
- Amount: 1

### 2_support

- Accuracy: medium
- Stability: high
- Amount: 2

### 3_mounting_plate

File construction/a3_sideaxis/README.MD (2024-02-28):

# Sideaxis

## 3D-Printing

### 1_side_axis_end_switch_holder_long

- Accuracy: medium (medium, 0.2)
- Stability: high (high, 50%)
- Amount: 1 (2)

### 2_side_axis_end_switch_holder

- Accuracy: medium (medium, 0.2)
- Stability: high (high, 50%)
- Amount: 1 (1)

### 3_side_axis_trapezoidal_spindle_bearing

- Accuracy: medium (medium, 0.2)
- Stability: medium (medium, 30%)
- Amout: 2 (2)

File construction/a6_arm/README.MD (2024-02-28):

# Arms

# Left Arm

## 3D-Printing

### 1_arm_top_left
- Accuracy: low
- Stability: low
- Amount: 1

### 2_arm_middle_left
- Accuracy: low
- Stability: low
- Amount: 1

### 3_arm_cameraholder
- Accuracy: low
- Stability: low
- Amount: 1

# Right Arm

### 5_arm_top_rechts
- Accuracy: low
- Stability: low
- Amount: 1

### 2_arm_middle
- Accuracy: low
- Stability: low
- Amount: 1

### 3_arm_bottom
- Accuracy: low
- Stability: low
- Amount: 1

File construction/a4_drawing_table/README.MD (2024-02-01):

# Paperholder

## 3D-Printing

### 1_paper_bottom
- Accuracy: medium
- Stability: medium
- Amount: 1

### 4_paper_bottom_2
- Accuracy: medium
- Stability: medium
- Amount: 2

### 2_paper_floor
- Accuracy: medium
- Stability: low / medium
- Amount: 1
- Kommentar: Schöne oberste Schicht wäre am wichtigsten

### 5_paper_floor_2
- Accuracy: medium
- Stability: low / medium
- Amount: 1
- Kommentar: Schöne oberste Schicht wäre am wichtigsten

### 3_paper_holder
- Accuracy: medium
- Stability: medium
- Amount: 8

### 7_paper_holder_cover
- Accuracy: low
- Stability: high
- Amount: 4

### 6_paper_holder_cover
- Accuracy: low
- Stability: high
- Amount: 4

### 8_paper_markers
- accuracy: low
- Stability: low
- Amount: 4
- Kommentar: Wenns geht weiß oder dunkelblaue Farbe

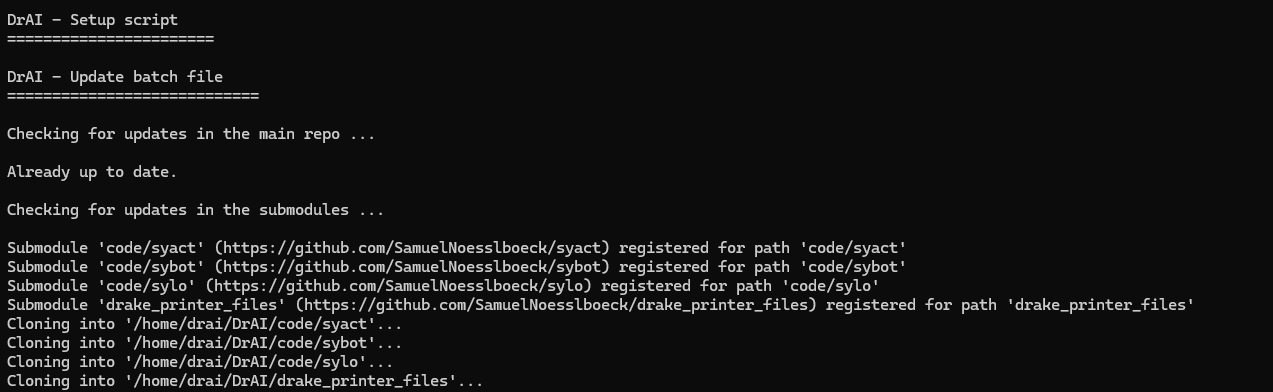
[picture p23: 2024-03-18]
documentation/images/project_description/setup_batch_file.PNG

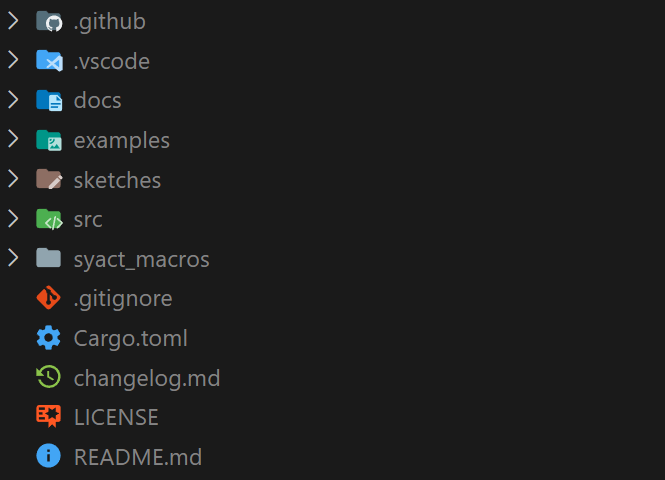
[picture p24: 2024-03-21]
documentation/images/project_description/rust_project_buildup.PNG

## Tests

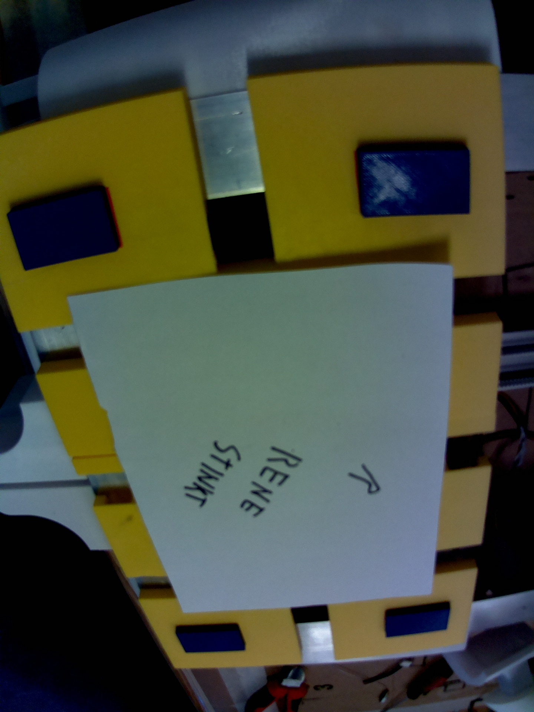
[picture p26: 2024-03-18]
code/ai_pipeline/images/testImages/IMAGE.jpg

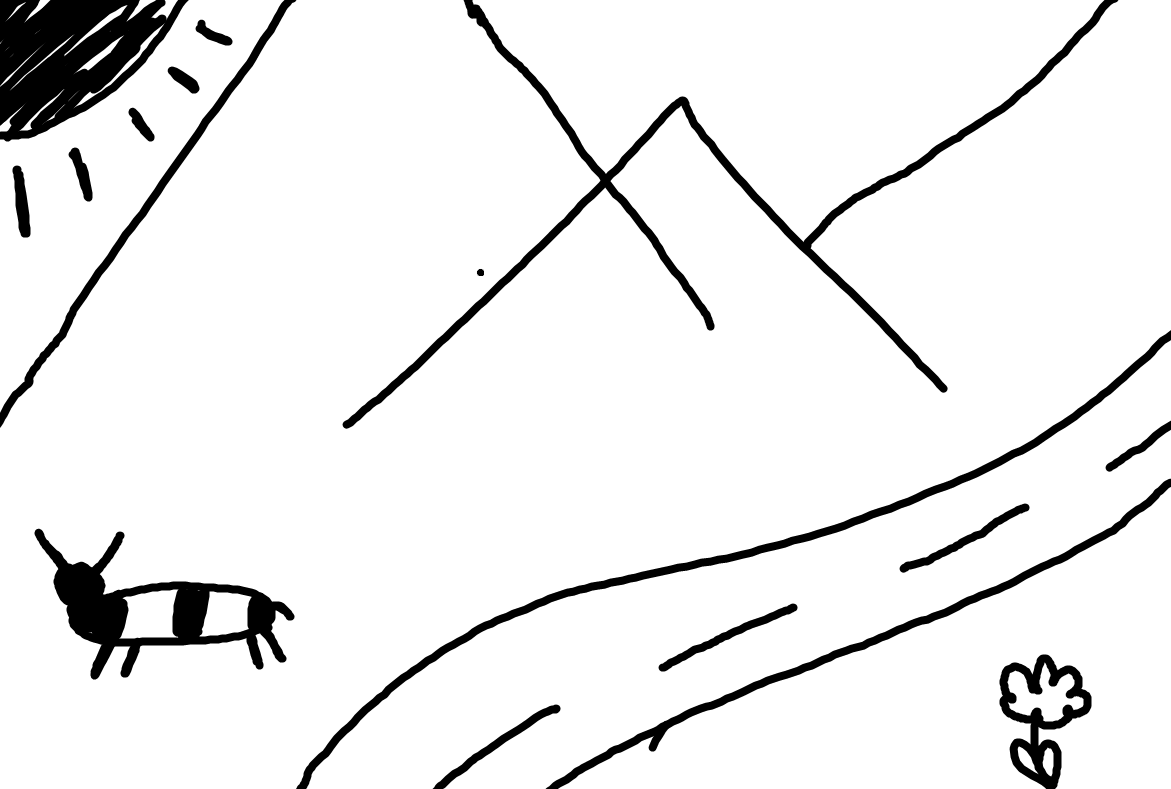
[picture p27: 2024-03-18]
code/ai_pipeline/images/testImages/test3.png

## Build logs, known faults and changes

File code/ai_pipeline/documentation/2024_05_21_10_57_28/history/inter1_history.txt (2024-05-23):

Input:

Output:
patent patent diagram, one - line drawing, one-line drawing, scene with machine gun, court drawing, with electric arc device, floorplan, line-drawing, floor plan, minimalist ink drawing of a city, drawn image, ( ( dithered ) ), one line drawing, plan drawing, architectural sketch, jpeg artifacts, asemic writing, single line drawing

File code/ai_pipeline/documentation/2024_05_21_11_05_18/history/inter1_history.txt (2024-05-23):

Input:

Output:
a diagram of a plane with a plane at the bottom, scene with machine gun, one-line drawing, one - line drawing, court drawing, minimalist ink drawing of a city, 18th century drawing, with electric arc device, single panel, single figure composition, face made of notation, plan drawing, jpeg artifacts

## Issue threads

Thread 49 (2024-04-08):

Rework meas-switches for X-Axis

SchwarzRene, 2024-04-08:

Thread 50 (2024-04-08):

Drawing head mounting part rework

SchwarzRene, 2024-04-08:

Closed 2024-04-08.

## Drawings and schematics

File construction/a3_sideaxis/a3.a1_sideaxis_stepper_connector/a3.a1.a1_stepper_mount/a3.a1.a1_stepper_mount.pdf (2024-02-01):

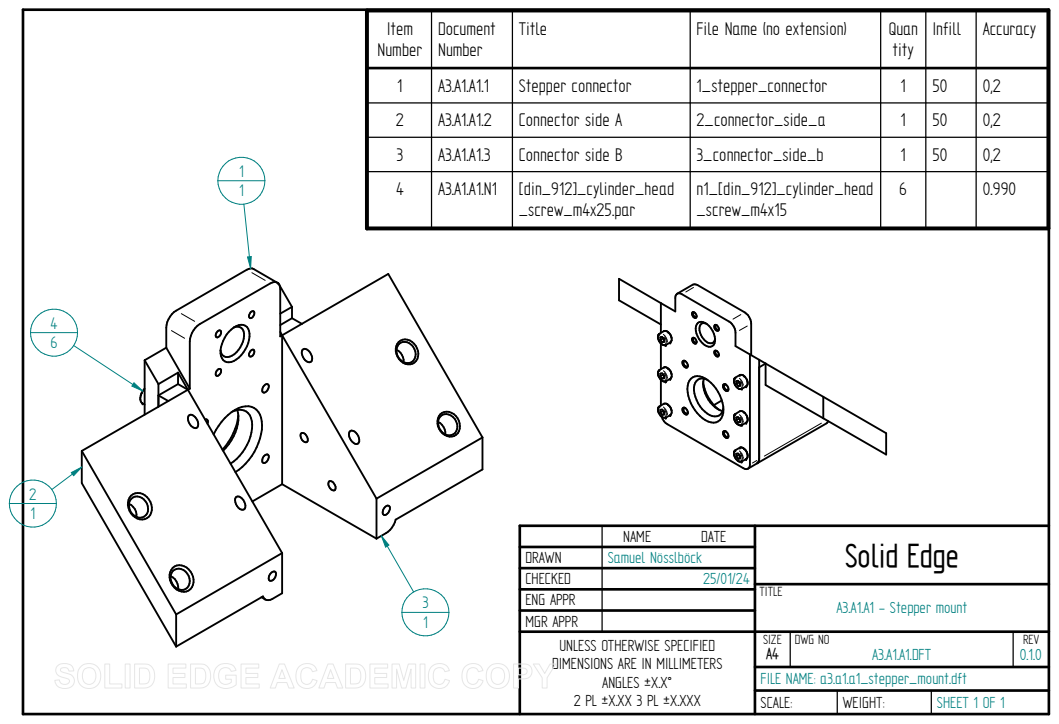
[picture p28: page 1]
TITLE; A3.A1.A1 - Stepper mount; SCALE:; WEIGHT:; SHEET 1 OF 1

Item Number | Document Number | Title | File Name (no extension) | Quan tity | Infill | Accuracy

1 | A3.A1.A1.1 | Stepper connector | 1_stepper_connector | 1 | 50 | 0,2
2 | A3.A1.A1.2 | Connector side A | 2_connector_side_a | 1 | 50 | 0,2
3 | A3.A1.A1.3 | Connector side B | 3_connector_side_b | 1 | 50 | 0,2
4 | A3.A1.A1.N1 | [din_912]_cylinder_head _screw_m4x25.par | n1_[din_912]_cylinder_head _screw_m4x15 | 6 | | 0.990

NAME DATE | Solid Edge

DRAWN | Samuel Nösslböck
CHECKED | 25/01/24
ENG APPR
MGR APPR
UNLESS OTHERWISE SPECIFIED DIMENSIONS ARE IN MILLIMETERS ANGLES ±X.X° 2 PL ±X.XX 3 PL ±X.XXX | SIZE A4 | DWG NO A3.A1.A1.DFT | REV 0.1.0

FILE NAME: a3.a1.a1_stepper_mount.dft

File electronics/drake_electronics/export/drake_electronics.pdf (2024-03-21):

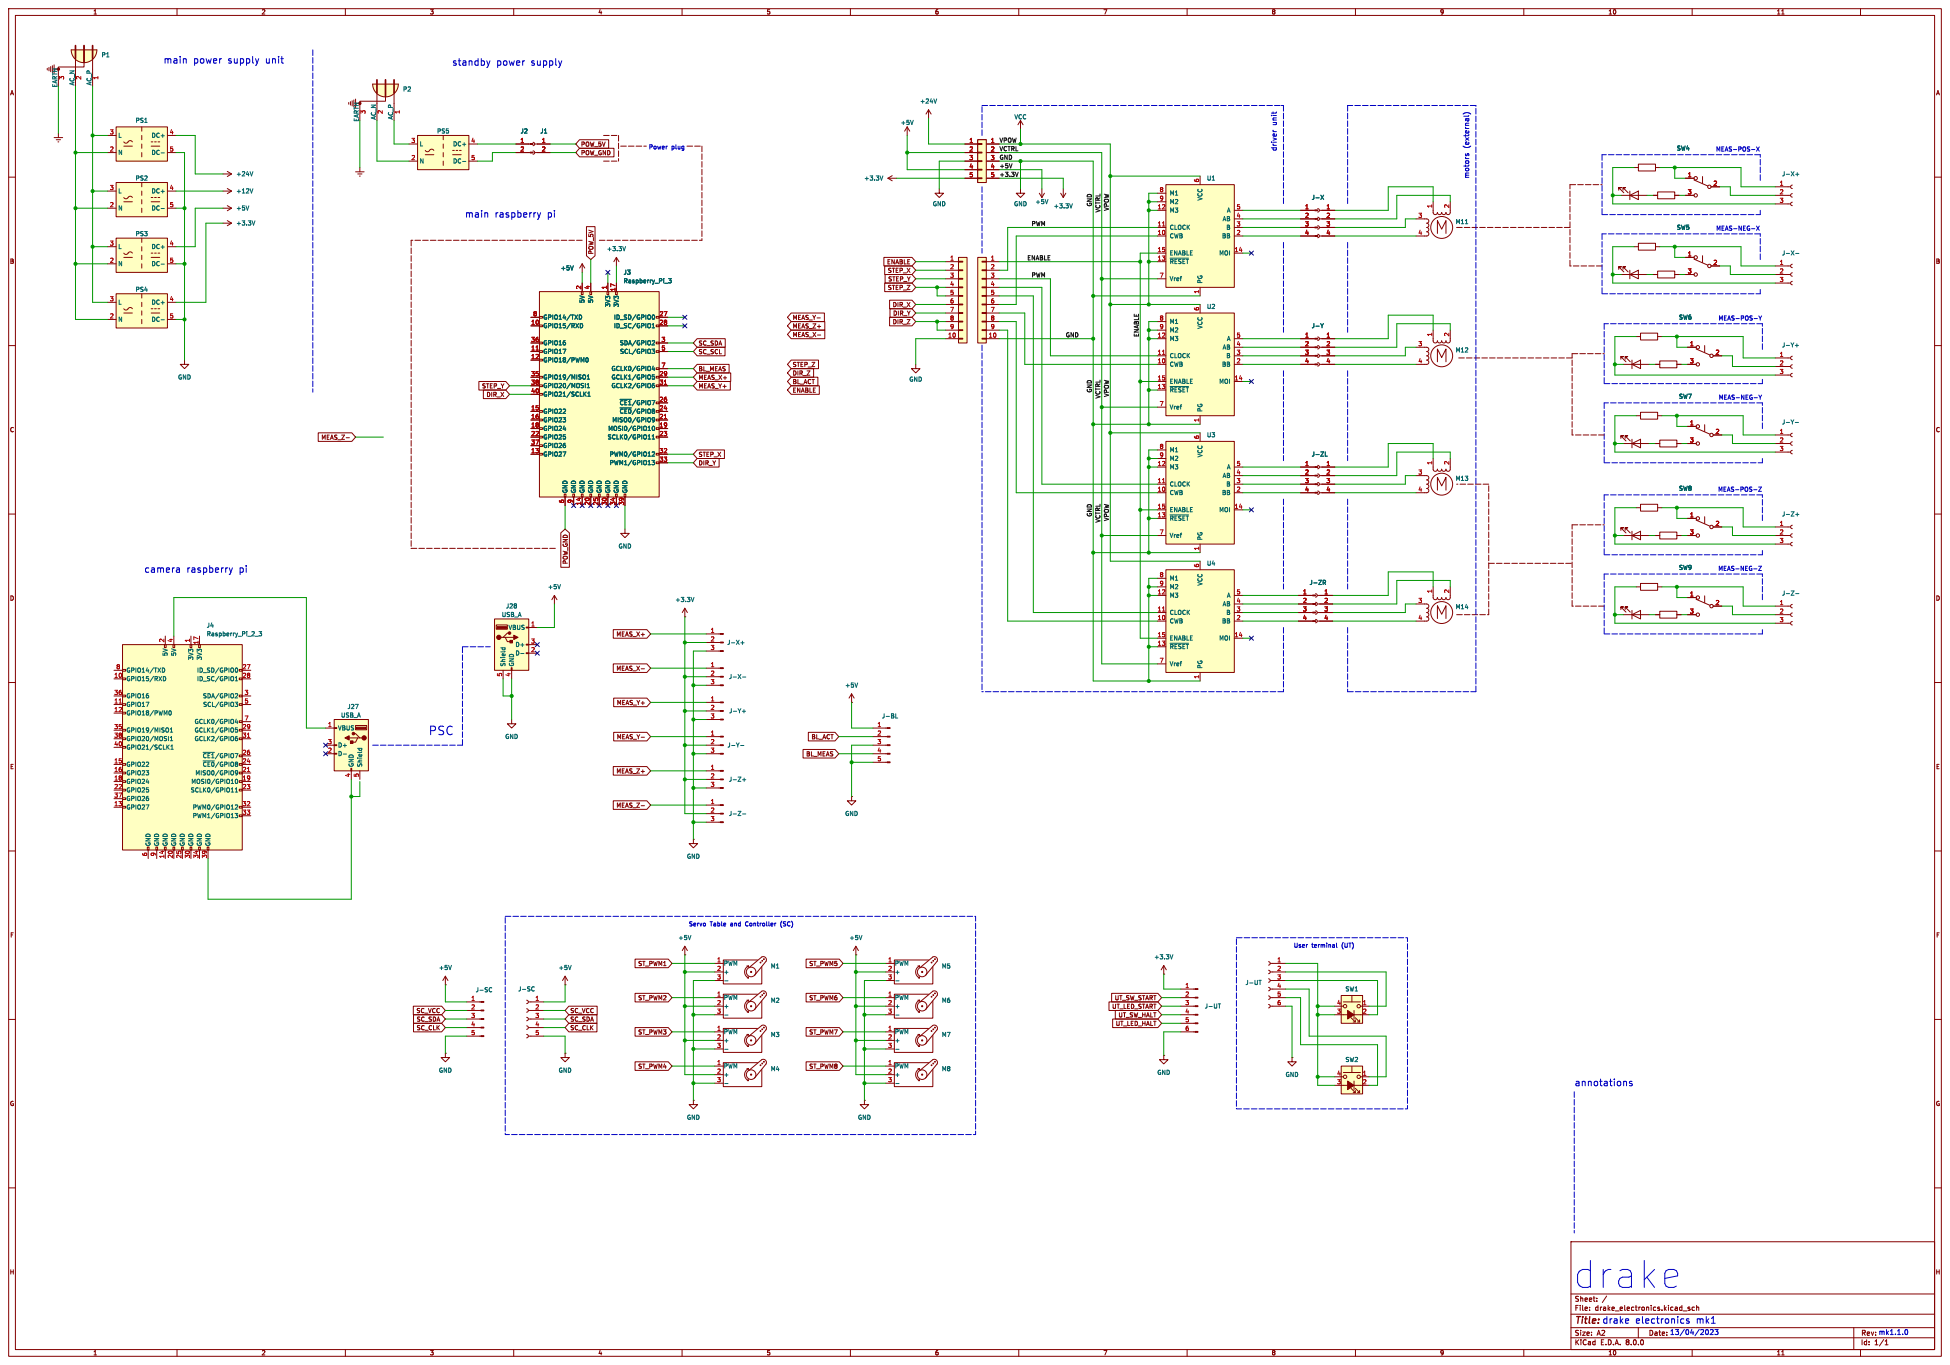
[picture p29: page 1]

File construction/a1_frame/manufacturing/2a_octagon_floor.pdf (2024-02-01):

B

A

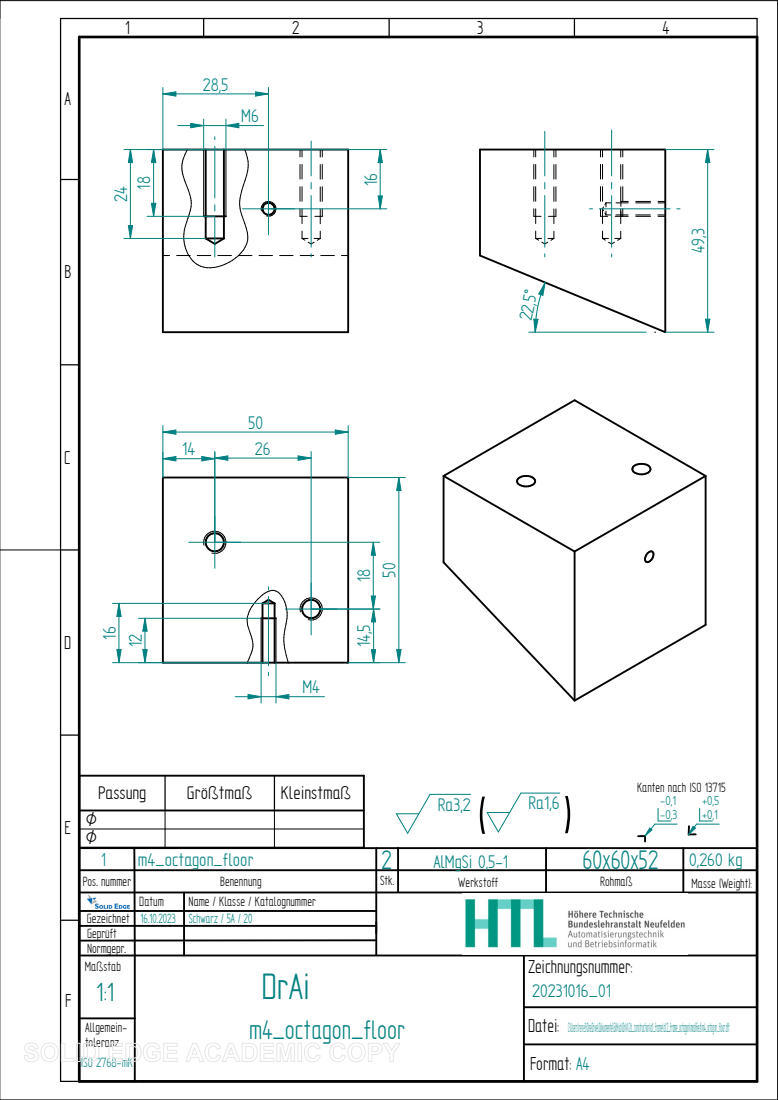
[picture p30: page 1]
Allgemein-; C:\Users\rene3\OneDrive\Dokumente\GitHub\DrAI\2d_construction\a1_frame\a1.2_frame_octagon\modified\m4_octagon_floor.dft; toleranz; ISO 2768-mK; Format: A4; Datei:; Kanten nach ISO 13715 -0,1 -0,3

Passung | Größtmaß | Kleinstmaß
1 | m4_octagon_floor | 2 | AlMgSi 0,5-1 | 60x60x52 | 0,260 kg
Pos. nummer | Benennung | | Werkstoff | Rohmaß | Masse (Weight): Stk.

Datum | Name / Klasse / Katalognummer
Maßstab 1:1 | DrAi m4_octagon_floor | Zeichnungsnummer: 20231016_01

Gezeichnet | 16.10.2023 | Schwarz / 5A / 20
Geprüft
Normgepr.

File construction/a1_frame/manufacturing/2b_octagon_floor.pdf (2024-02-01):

B

A

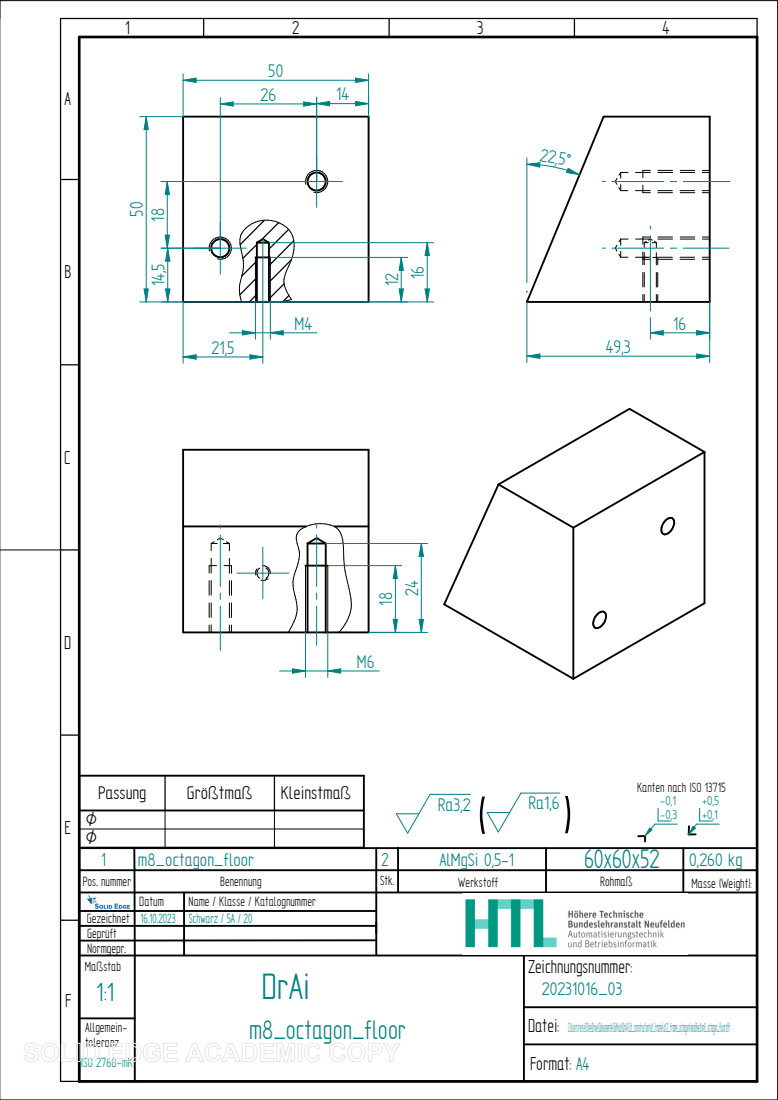
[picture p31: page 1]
Allgemein-; C:\Users\rene3\OneDrive\Dokumente\GitHub\DrAI\2d_construction\a1_frame\a1.2_frame_octagon\modified\m8_octagon_floor.dft; toleranz; ISO 2768-mK; Format: A4; Datei:; Kanten nach ISO 13715 -0,1 -0,3

Passung | Größtmaß | Kleinstmaß
1 | m8_octagon_floor | 2 | AlMgSi 0,5-1 | 60x60x52 | 0,260 kg
Pos. nummer | Benennung | | Werkstoff | Rohmaß | Masse (Weight): Stk.

Datum | Name / Klasse / Katalognummer
Maßstab 1:1 | DrAi m8_octagon_floor | Zeichnungsnummer: 20231016_03

Gezeichnet | 16.10.2023 | Schwarz / 5A / 20
Geprüft
Normgepr.

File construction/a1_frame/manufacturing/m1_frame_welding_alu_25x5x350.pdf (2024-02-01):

B

A

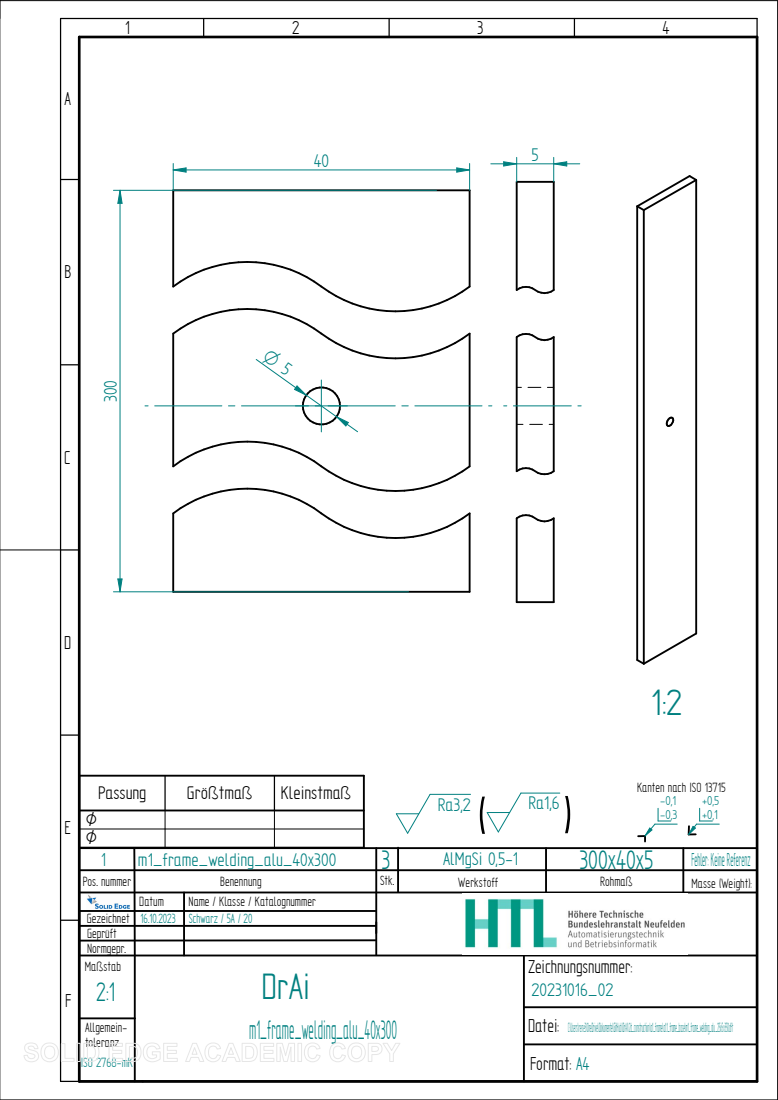
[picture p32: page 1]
Allgemein-; C:\Users\rene3\OneDrive\Dokumente\GitHub\DrAI\2d_construction\a1_frame\a1.1_frame_base\m1_frame_welding_alu_25x5x350.dft; toleranz; ISO 2768-mK; Format: A4; Datei:; Kanten nach ISO 13715 -0,1 -0,3

Passung | Größtmaß | Kleinstmaß
1 | m1_frame_welding_alu_40x300 | 3 | AlMgSi 0,5-1 | 300x40x5 | Fehler: Keine Referenz
Pos. nummer | Benennung | | Werkstoff | Rohmaß | Masse (Weight): Stk.

Datum | Name / Klasse / Katalognummer
Maßstab 2:1 | DrAi m1_frame_welding_alu_40x300 | Zeichnungsnummer: 20231016_02

Gezeichnet | 16.10.2023 | Schwarz / 5A / 20
Geprüft
Normgepr.

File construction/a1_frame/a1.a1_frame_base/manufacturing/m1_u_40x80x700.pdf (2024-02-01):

B | B
A | A

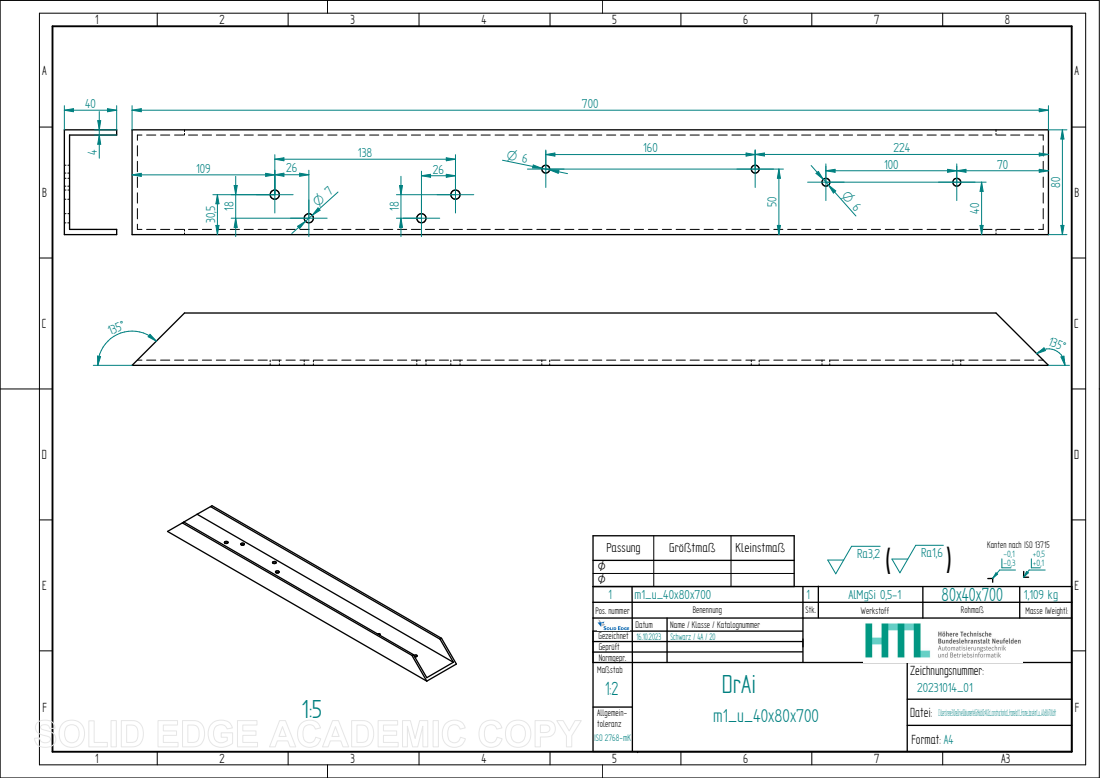
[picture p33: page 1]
Allgemein-; C:\Users\rene3\OneDrive\Dokumente\GitHub\DrAI\2d_construction\a1_frame\a1.1_frame_base\m1_u_40x80x700.dft; toleranz; ISO 2768-mK; Format: A4; Datei:; Kanten nach ISO 13715 -0,1 -0,3

Passung | Größtmaß | Kleinstmaß
1 | m1_u_40x80x700 | 1 | AlMgSi 0,5-1 | 80x40x700 | 1,109 kg
Pos. nummer | Benennung | | Werkstoff | Rohmaß | Masse (Weight): Stk.

Datum | Name / Klasse / Katalognummer
Maßstab 1:2 | DrAi m1_u_40x80x700 | Zeichnungsnummer: 20231014_01

Gezeichnet | 16.10.2023 | Schwarz / 4A / 20
Geprüft
Normgepr.

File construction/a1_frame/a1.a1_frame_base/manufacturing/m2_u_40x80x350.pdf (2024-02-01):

B | B
A | A

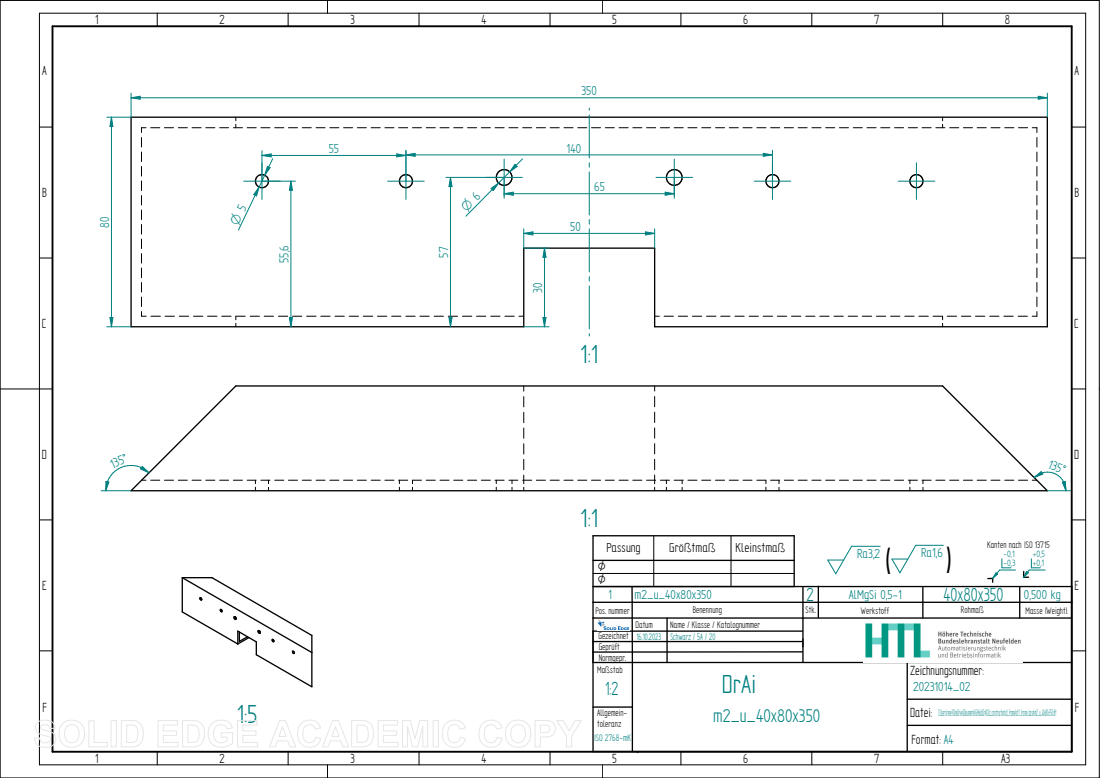
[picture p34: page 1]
Allgemein-; C:\Users\rene3\OneDrive\Dokumente\GitHub\DrAI\2d_construction\a1_frame\a1.1_frame_base\m2_u_40x80x350.dft; toleranz; ISO 2768-mK; Format: A4; Datei:; Kanten nach ISO 13715 -0,1 -0,3

Passung | Größtmaß | Kleinstmaß
1 | m2_u_40x80x350 | 2 | AlMgSi 0,5-1 | 40x80x350 | 0,500 kg
Pos. nummer | Benennung | | Werkstoff | Rohmaß | Masse (Weight): Stk.

Datum | Name / Klasse / Katalognummer
Maßstab 1:2 | DrAi m2_u_40x80x350 | Zeichnungsnummer: 20231014_02

Gezeichnet | 16.10.2023 | Schwarz / 5A / 20
Geprüft
Normgepr.

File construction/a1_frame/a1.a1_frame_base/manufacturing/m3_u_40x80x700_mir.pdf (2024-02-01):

B | B
A | A

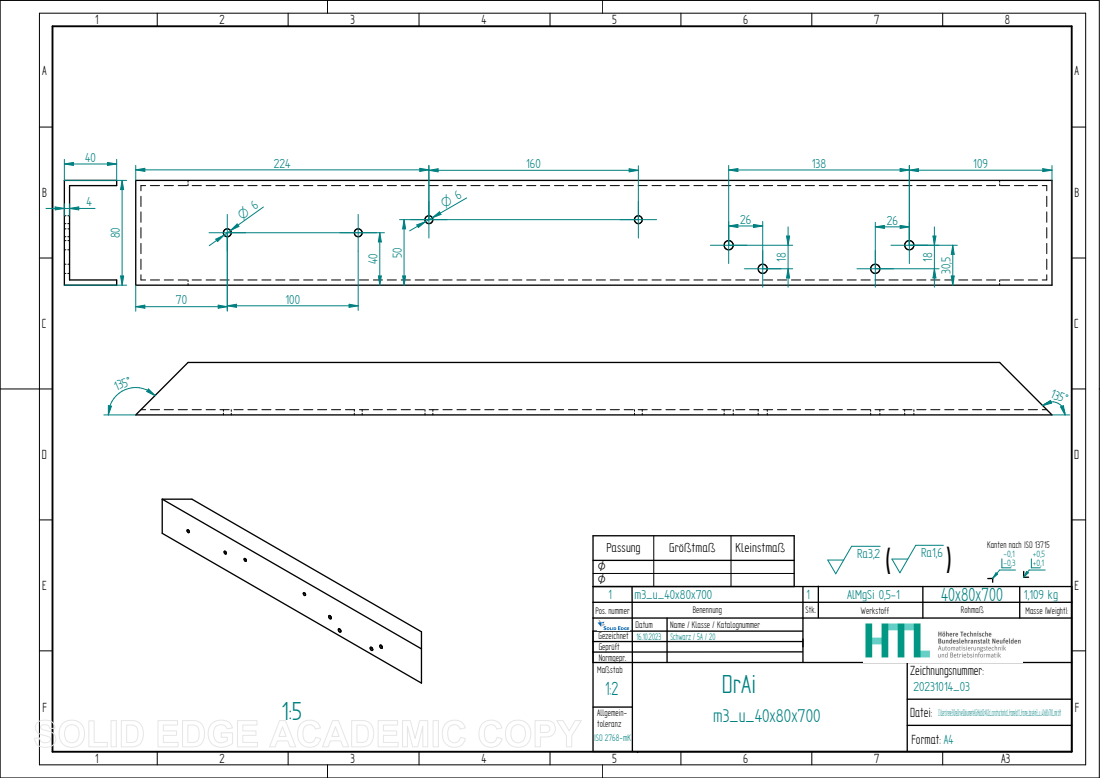
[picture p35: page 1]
Allgemein-; C:\Users\rene3\OneDrive\Dokumente\GitHub\DrAI\2d_construction\a1_frame\a1.1_frame_base\m3_u_40x80x700_mir.dft; toleranz; ISO 2768-mK; Format: A4; Datei:; Kanten nach ISO 13715 -0,1 -0,3

Passung | Größtmaß | Kleinstmaß
1 | m3_u_40x80x700 | 1 | AlMgSi 0,5-1 | 40x80x700 | 1,109 kg
Pos. nummer | Benennung | | Werkstoff | Rohmaß | Masse (Weight): Stk.

Datum | Name / Klasse / Katalognummer
Maßstab 1:2 | DrAi m3_u_40x80x700 | Zeichnungsnummer: 20231014_03

Gezeichnet | 16.10.2023 | Schwarz / 5A / 20
Geprüft
Normgepr.

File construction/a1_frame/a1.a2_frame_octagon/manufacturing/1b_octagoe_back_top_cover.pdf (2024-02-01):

B | B
A | A

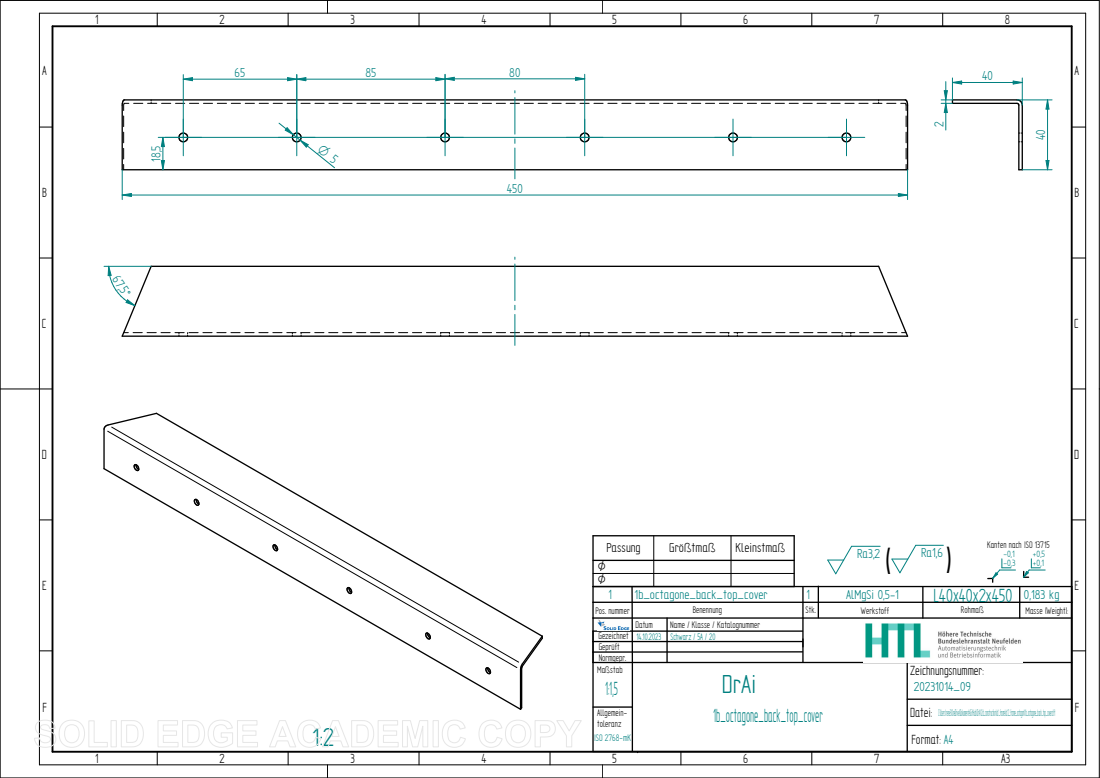
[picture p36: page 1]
Allgemein-; C:\Users\rene3\OneDrive\Dokumente\GitHub\DrAI\2d_construction\a1_frame\a1.2_frame_octagon\1b_octagone_back_top_cover.dft; toleranz; ISO 2768-mK; Format: A4; Datei:; Kanten nach ISO 13715 -0,1 -0,3

Passung | Größtmaß | Kleinstmaß
1 | 1b_octagone_back_top_cover | 1 | AlMgSi 0,5-1 | L40x40x2x450 | 0,183 kg
Pos. nummer | Benennung | | Werkstoff | Rohmaß | Masse (Weight): Stk.

Datum | Name / Klasse / Katalognummer
Maßstab 1:1,5 | DrAi 1b_octagone_back_top_cover | Zeichnungsnummer: 20231014_09

Gezeichnet | 14.10.2023 | Schwarz / 5A / 20
Geprüft
Normgepr.

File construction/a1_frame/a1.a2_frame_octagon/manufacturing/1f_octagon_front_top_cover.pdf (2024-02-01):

B | B
A | A

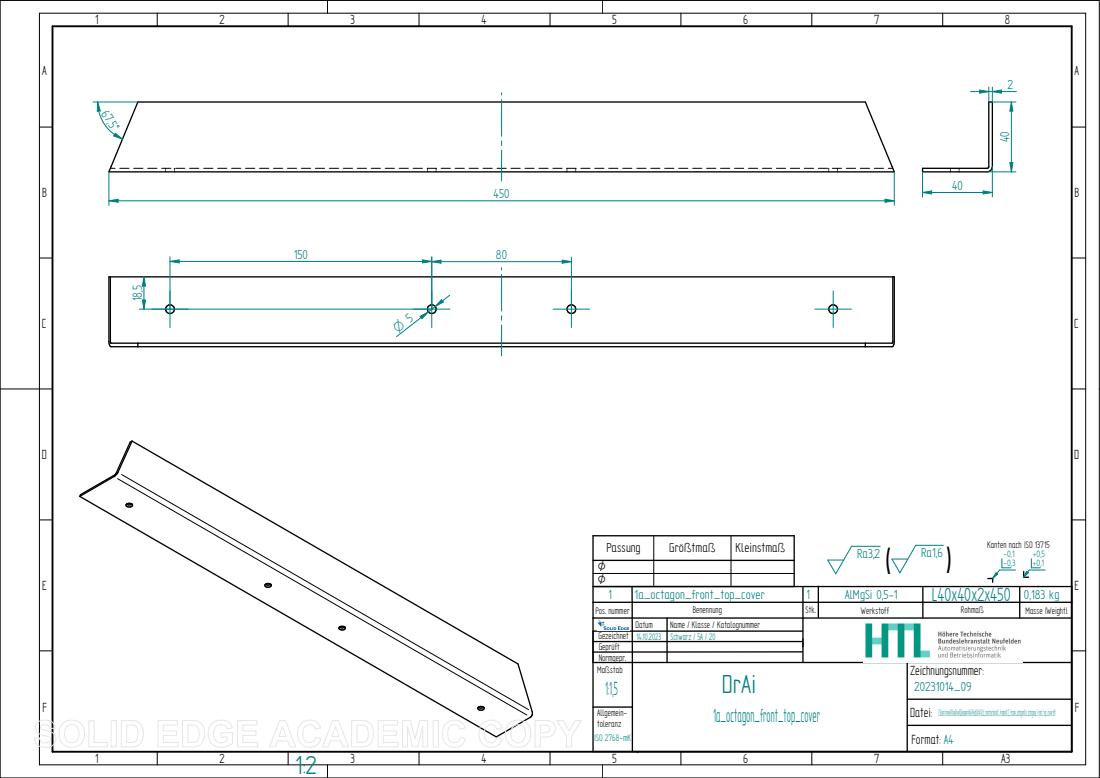
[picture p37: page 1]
Allgemein-; C:\Users\rene3\OneDrive\Dokumente\GitHub\DrAI\2d_construction\a1_frame\a1.2_frame_octagon\1a_octagone_front_top_cover.dft; toleranz; ISO 2768-mK; Format: A4; Datei:; Kanten nach ISO 13715 -0,1 -0,3

Passung | Größtmaß | Kleinstmaß
1 | 1a_octagon_front_top_cover | 1 | AlMgSi 0,5-1 | L40x40x2x450 | 0,183 kg
Pos. nummer | Benennung | | Werkstoff | Rohmaß | Masse (Weight): Stk.

Datum | Name / Klasse / Katalognummer
Maßstab 1:1,5 | DrAi 1a_octagon_front_top_cover | Zeichnungsnummer: 20231014_09

Gezeichnet | 14.10.2023 | Schwarz / 5A / 20
Geprüft
Normgepr.

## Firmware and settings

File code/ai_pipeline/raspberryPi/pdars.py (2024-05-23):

import matplotlib.pyplot as plt
import numpy as np
import requests
import json
import cv2

def drawPoints( img, points ):
    imgCopy = np.copy( img )

    for point in points:
        imgCopy = cv2.circle( imgCopy, ( int( point[ 0 ] ), int( point[ 1 ] ) ), 10, ( 255, 255, 0 ), -1 )

    cv2.imshow( "", imgCopy )
    cv2.waitKey( 0 )

def img2Hsv( img ):
    img = cv2.cvtColor( img, cv2.COLOR_BGR2HSV )
    return img

def markerDetection( img, h = ( 10, 100 ), s = ( 10, 20 ), v = ( 0, 255 ) ):
    blackWhiteImg = np.where( ( ( img[ :, :, 0 ] >= h[ 0 ] ) & ( img[ :, :, 0 ] <= h[ 1 ] ) 
                              & ( img[ :, :, 1 ] >= s[ 0 ] ) & ( img[ :, :, 1 ] <= s[ 1 ] )
                              & ( img[ :, :, 2 ] >= v[ 0 ] ) & ( img[ :, :, 2 ] <= v[ 1 ] )  ), 255, 0 )
    
    return blackWhiteImg.astype( np.uint8 )
    
def detectCorners( img ):
    dst = cv2.cornerHarris( img, 15, 21, 0.15 )
    dst = cv2.dilate(dst,None)
    _, dst = cv2.threshold(dst,0.1*dst.max(),255,0)
    dst = np.uint8(dst)

    indexes = np.where( dst == 255 )
    return indexes

def getL2DistToPoint( point, indexes ):
    point = np.array( point ).reshape( -1, 2 )

    yCords = indexes[ 0 ].reshape( -1, 1 )
    xCords = indexes[ 1 ].reshape( -1, 1 )

    cords = np.concatenate( [ yCords, xCords ], axis = -1 )

    distances = np.sum( ( cords - point ) ** 2, axis = -1 ) ** 0.5

    return distances

def getL2Distances( indexes, imgShape ): 
    topLeftDist = getL2DistToPoint( [ 0, 0 ], indexes )
    topRightDist = getL2DistToPoint( [ 0, imgShape[ 1 ] ], indexes )

    bottomLeftDist = getL2DistToPoint( [ imgShape[ 0 ], 0 ], indexes )
    bottomRightDist = getL2DistToPoint( [ imgShape[ 0 ], imgShape[ 1 ] ], indexes )

    return ( topLeftDist, topRightDist, bottomRightDist, bottomLeftDist )

def minL2Dist( distance ):
    return np.argmin( distance )

def transform( img, corners, device = "plattform" ):
    global SETTINGS
    ################################
    # Transform the image
    # coordinates to order: top-left, top-right, bottom-right, bottom-left

    if device == "plattform":
        maxWidth = SETTINGS[ "plattformWidth" ] * 3
        maxHeight = SETTINGS[ "plattformHeight" ] * 3
    else:
        maxWidth = SETTINGS[ "paperWidth" ] * 3
        maxHeight = SETTINGS[ "paperHeight" ] * 3

    destination_corners = [[0, 0], [maxWidth, 0], [maxWidth, maxHeight], [0, maxHeight]]

    corners = np.concatenate( [ np.expand_dims( corners[ :, 1 ], axis = -1 ), np.expand_dims( corners[ :, 0 ], axis = -1 ) ], axis = -1 )


    M = cv2.getPerspectiveTransform(np.float32(corners), np.float32(destination_corners))
    final = cv2.warpPerspective( img, M, (destination_corners[2][0], destination_corners[2][1]), flags=cv2.INTER_LINEAR)

    return final

def cornerDistances( indexes, imgWidth, imgHeight ):
    """
    return a list with the x, y coordinates of the points and a tuple consisting of the indexes of the 
    [ { "x": .., "y": .. }, {}.. ], ( top-left-corner, top-right-corner, bottom-left-corner, bottom-right-corner )
    """
    cornerDistances = []
    cornerPositions = []

    #Image Corners sorted by top-left, top-right, bottom-left, bottom-right
    imagePoints = np.array( [ [ 0, 0 ], [ imgWidth, 0 ], [ 0, imgHeight ], [ imgWidth, imgHeight ] ] )


    for i in range( len( indexes[ 0 ] ) ):
        y = indexes[ 0 ][ i ]; x = indexes[ 1 ][ i ]

        p = np.array( [ x, y ] )

        distances = np.sum( ( imagePoints - p ) ** 2, axis = -1 ) ** 0.5

        cornerDistances.append( distances )
        cornerPositions.append( { "x": x, "y": y } )

    cornerDistances = np.array( cornerDistances ).reshape( len( cornerDistances ), 4 )

    topLeftCorner = np.argmin( cornerDistances[ :, 0 ] )
    topRightCorner = np.argmin( cornerDistances[ :, 1 ] )
    bottomLeftCorner = np.argmin( cornerDistances[ :, 2 ] )
    bottomRightCorner = np.argmin( cornerDistances[ :, 3 ] )

    return cornerPositions, ( topLeftCorner, topRightCorner, bottomLeftCorner, bottomRightCorner )

def getDistanceToPoint( a, b ):
    """
    Get the l2 distances of two arrays where each array consists of ( -1, 2 ) and the coordinates are aranged in x, y
    """
    a = np.expand_dims( a, axis = 1 )
    b = np.expand_dims( b, axis = 0 )

    distances = np.sum( ( a - b ) ** 2, axis = -1 ) ** 0.5
    return distances
    
def undisturbImg( img, points ):
    markerPoints, _ = points

    realWorldCoords = []
    
    for m_x in range( 2 ):
        for m_y in range( 2 ):

            for x in range( 2 ):
                for y in range( 2 ):
                    p_x = m_x * SETTINGS[ "plattformWidth" ] + ( ( -1 ) ** m_x ) * x * SETTINGS[ "marker-width" ]
                    p_y = m_y * SETTINGS[ "plattformHeight" ] + ( ( -1 ) ** m_y ) * y * SETTINGS[ "marker-height" ]

                    realWorldCoords.append( [ p_x, p_y ] )

    realWorldCoords = np.reshape( realWorldCoords, ( -1, 2 ) )

    objp = np.zeros((1, 16, 3), np.float32)
    objp[0,:,:2] = realWorldCoords

    imageCorners = np.array( [
        [ 0, 0 ],
        [ 0, img.shape[ 1 ] ],
        [ img.shape[ 0 ], 0 ],
        [ img.shape[ 0 ], img.shape[ 1 ] ]
    ])

    markerCenters = np.mean( markerPoints, axis = 1 )

    d = getDistanceToPoint( imageCorners, markerCenters )

    newMarkerPoints = np.zeros_like( markerPoints )
    arangedMarkerCenters = []

    for i in range( 4 ):
        newMarkerPoints[ i ][ :, : ] = markerPoints[ np.argmin( d[ i ] ) ][ :, : ]
        arangedMarkerCenters.append( markerCenters[ np.argmin( d[ i ] ) ] )

    markerPoints = newMarkerPoints

    paperCenter = np.expand_dims( np.mean( markerCenters, axis = 0 ), axis = 0 )

    arangedPoints = np.zeros( ( 16, 2 ), np.float32 )
    for mCIdx in range( 4 ):
        d = getDistanceToPoint( paperCenter, markerPoints[ mCIdx ] )

        #Detect marker points
        #P1 is outher marker point
        #P4 is inner marker point
        p1 = markerPoints[ mCIdx ][ np.argmax( d, axis = -1 ) ]
        p4 = markerPoints[ mCIdx ][ np.argmin( d, axis = -1 ) ]

        #Detect p2
        if mCIdx == 0 or mCIdx == 1:
            sideMiddle = ( arangedMarkerCenters[ 0 ] + arangedMarkerCenters[ 1 ] ) / 2
            sideMiddle[ 0 ] -= 100
        else:
            sideMiddle = ( arangedMarkerCenters[ 2 ] + arangedMarkerCenters[ 3 ] ) / 2
            sideMiddle[ 0 ] += 100

        sideMiddle = np.expand_dims( sideMiddle, axis = 0 )

        d = getDistanceToPoint( sideMiddle, markerPoints[ mCIdx ] )
        p2 = markerPoints[ mCIdx ][ np.argmin( d, axis = -1 ) ]     

        #Detect P3
        if mCIdx == 0 or mCIdx == 2:
            sideMiddle = ( arangedMarkerCenters[ 0 ] + arangedMarkerCenters[ 2 ] ) / 2 
            sideMiddle[ 1 ] -= 100
        else:
            sideMiddle = ( arangedMarkerCenters[ 1 ] + arangedMarkerCenters[ 3 ] ) / 2 #
            sideMiddle[ 1 ] += 100

        sideMiddle = np.expand_dims( sideMiddle, axis = 0 )

        d = getDistanceToPoint( sideMiddle, markerPoints[ mCIdx ] )
        p3 = markerPoints[ mCIdx ][ np.argmin( d, axis = -1 ) ]   

        arangedPoints[  mCIdx * 4 : ( mCIdx + 1 ) * 4 ] = np.squeeze( np.array( [ p1, p2, p3, p4 ] ), axis = 1 )

    arangedPoints = np.reshape( arangedPoints, ( 1, -1, 2 ) )

    ret, mtx, dist, rvecs, tvecs = cv2.calibrateCamera( objp, arangedPoints, ( img.shape[ 1 ], img.shape[ 0 ] ), None, None)
    dst = cv2.undistort( img, mtx, dist, None, mtx )

    return dst

def markerPlattformCoords( img, resultImg = False, loadCopy = False ):
    global SETTINGS

    if loadCopy:
        SETTINGS = json.load( open( "./config_copy.json", "r" ) )

    img = img2Hsv( img )

    markerImg = markerDetection( img, ( SETTINGS[ "markers" ][ "h-min" ], SETTINGS[ "markers" ][ "h-max" ] ), ( SETTINGS[ "markers" ][ "s-min" ], SETTINGS[ "markers" ][ "s-max" ] ) )
    
    canny = markerImg.astype( np.uint8 )
    
    contours, _ = cv2.findContours(image=canny, mode=cv2.RETR_EXTERNAL, method=cv2.CHAIN_APPROX_NONE)

    areas = []
    for i in range( len( contours ) ):
        c = contours[ i ]

        area = cv2.contourArea(c)
        if area > 500:
            areas.append( { "areas": area, "idx": i } )


    markerCenters = []
    markerPoints = []

    sortedValues = []
    print( f"Found {len(areas)} which could be markers" )
    for i in range( len( areas ) ):
        approx = cv2.approxPolyDP( contours[ areas[ i ][ "idx" ] ], 0.04 * cv2.arcLength(contours[ areas[ i ][ "idx" ] ], True), True) 
        centerApprox = np.reshape( approx, ( -1, 2 ) )

        rect = cv2.minAreaRect( contours[ areas[ i ][ "idx" ] ] )
        box = cv2.boxPoints(rect)
        box = box.astype( np.int32 )
        
        length = np.sum( ( box[ 0 ] - box[ 1 ] ) ** 2 ) ** 0.5
        width = np.sum( ( box[ 1 ] - box[ 2 ] ) ** 2 ) ** 0.5

        scope = ( length + width ) * 2
        boxArea = length * width

        contourScope = cv2.arcLength( contours[ areas[ i ][ "idx" ] ], True )
        
        if len( centerApprox ) >= 4:
            p = 1 - abs( 1 - boxArea / cv2.contourArea( contours[ areas[ i ][ "idx" ] ] ) ) *  abs( 1 - scope / contourScope )
            sortedValues.append( { "idx": len( markerPoints ), "v": p } )

            markerPoints.append( centerApprox )
            
            center = np.sum( centerApprox, axis = 0 ) / len( approx )
            markerCenters.append( center )
    
    sortedValues = sorted( sortedValues, key = lambda x: x[ "v" ], reverse = True )

    foundMarkerPoints = []
    foundMarkerCenters = []
    for i in range( min( 4, len( sortedValues ) ) ):
        idx = sortedValues[ i ][ "idx" ]

        foundMarkerPoints.append( markerPoints[ idx ] )
        foundMarkerCenters.append( markerCenters[ idx ] )

        #drawPoints( img, markerPoints[ idx ] )
                    
    markerCenters = foundMarkerCenters
    markerPoints = foundMarkerPoints

    markerCenters = np.reshape( markerCenters, ( -1, 2 ) )
    
    paperCenter = np.sum( markerCenters, axis = 0 ) / max( len( markerCenters ), 1 )

    if resultImg:
        return markerImg

    if len( markerPoints ) == 4:
        return ( markerPoints, paperCenter )
    else:
        raise ValueError( f"Marker Points have not the right shape, found {len(markerPoints)}" )

def getOutherPlattformPoints( img, markerPoints, paperCenter ):
    cornerPoints = []
    for j in range( len( markerPoints ) ): 
        distances = np.sum( ( paperCenter - markerPoints[ j ] ) ** 2, -1 ) ** 0.5

        point = markerPoints[ j ][ np.argmax( distances ) ]
        
        cornerPoints.append( point )

    cornerPoints = np.reshape( cornerPoints, ( -1, 2 ) )

    y = cornerPoints[ :, 1 ]; x = cornerPoints[ :, 0 ]
    cornerIndexes = [ y, x ]

    distances = getL2Distances( cornerIndexes, img.shape )

    #Get point index with the minimum l2 distance
    #pointidxs is a list of minimum distances aranged in the order like distances
    pointIdxs = [ minL2Dist( distances[ i ] ) for i in range( len( distances ) ) ]
    
    #get the coordinates of the points 
    cornerPoints = [ ( cornerIndexes[ 0 ][ pointIdxs[ i ] ], cornerIndexes[ 1 ][ pointIdxs[ i ] ] ) for i in range( len( distances ) ) ]
    cornerPoints = np.array( cornerPoints ).reshape( -1, 2 )

    return cornerPoints

def getPaperCorners( img, resultImg = False, loadCopy = False ):
    global SETTINGS
    if loadCopy:
        SETTINGS = json.load( open( "./config_copy.json", "r" ) )

    img = cv2.cvtColor( img, cv2.COLOR_BGR2HSV )

    paperImg = markerDetection( img, ( SETTINGS[ "plattform" ][ "h-min" ], SETTINGS[ "plattform" ][ "h-max" ] ), ( SETTINGS[ "plattform" ][ "s-min" ], SETTINGS[ "plattform" ][ "s-max" ] ) )

    if resultImg:
        return paperImg
    
    #If you remove that dont forget to remove the -20 in the bottom in line 313

    paddedImg = np.zeros( ( paperImg.shape[ 0 ] + 40, paperImg.shape[ 1 ] + 40 ), dtype = np.uint8 )
    paddedImg[ 20:-20, 20:-20 ] = paperImg
    
    canny = cv2.Canny( paddedImg, 20, 255 )

    canny = cv2.blur( canny, ( 3, 3 ) )

    canny = np.where( canny > 40, 255, 0 )
    canny = canny.astype( np.uint8 )

    contours, _ = cv2.findContours(image=canny, mode=cv2.RETR_EXTERNAL, method=cv2.CHAIN_APPROX_NONE)

    areas = []
    for i in range( len( contours ) ):
        c = contours[ i ]

        area = cv2.contourArea(c)

        areas.append( { "areas": area, "idx": i } )

    areas = sorted( areas, key = lambda x: x[ "areas" ], reverse=True )

    try:
        paperIdx = areas[ 0 ][ "idx" ]

        approx = cv2.approxPolyDP( contours[ paperIdx ], 0.04 * cv2.arcLength(contours[ paperIdx ], True), True) 

        coords = np.reshape( approx, ( -1, 2 ) ) - 20

        cornerIndexes = [ coords[ :, 1 ], coords[ :, 0 ] ]
        distances = getL2Distances( cornerIndexes, canny.shape )

        #Get point index with the minimum l2 distance
        #pointidxs is a list of minimum distances aranged in the order like distances
        pointIdxs = [ minL2Dist( distances[ i ] ) for i in range( len( distances ) ) ]
        
        #get the coordinates of the points 
        cornerPoints = [ ( cornerIndexes[ 0 ][ pointIdxs[ i ] ], cornerIndexes[ 1 ][ pointIdxs[ i ] ] ) for i in range( len( distances ) ) ]
        cornerPoints = np.array( cornerPoints ).reshape( -1, 2 )

        if cornerPoints.shape == ( 4, 2 ):
            return cornerPoints 
        else:
            "a" + 3
        
    except:
        raise ValueError( "Error detecting the paper" )

def getCoords( img ):
    #Detect the plattform in the retransformed img and get the outher points
    a, b = markerPlattformCoords( img )
    plattformCords = getOutherPlattformPoints( img, a, b )

    plattformImg = transform( img, plattformCords, device = "plattform" )

    paperCoords = getPaperCorners( plattformImg )

    return ( plattformCords, paperCoords )

def radtodeg( angle ):
    return angle / ( 2 * np.math.pi ) * 360

def getRealWorldPaperPoints( coords, imgWidth, imgHeight ):
    global SETTINGS
    top_left_paper_point = coords[ 1 ][ 0 ]
    top_right_paper_point = coords[ 1 ][ 1 ]
    bottom_right_paper_point = coords[ 1 ][ 2 ]
    bottom_left_paper_point = coords[ 1 ][ 3 ]

    paperRotation = np.arctan2( ( bottom_right_paper_point[ 0 ] - bottom_left_paper_point[ 0 ] ), bottom_right_paper_point[ 1 ] - bottom_left_paper_point[ 1 ] )

    offsetYBottomLeft = ( imgHeight - bottom_left_paper_point[ 0 ] ) / imgHeight * SETTINGS[ "plattformHeight" ]
    offsetXBottomLeft = (  bottom_left_paper_point[ 1 ] ) / imgWidth * SETTINGS[ "plattformWidth" ]

    offsetYTopLeft = ( top_left_paper_point[ 0 ] ) / imgHeight * SETTINGS[ "plattformHeight" ]
    offsetXTopLeft = ( top_left_paper_point[ 1 ] ) / imgWidth * SETTINGS[ "plattformWidth" ]

    offsetYTopRight = ( top_right_paper_point[ 0 ] ) / imgHeight * SETTINGS[ "plattformHeight" ]
    offsetXTopRight = (  imgWidth - top_right_paper_point[ 1 ] ) / imgWidth * SETTINGS[ "plattformWidth" ]

    offsetYBottomRight = ( imgHeight - bottom_right_paper_point[ 0 ] ) / imgHeight * SETTINGS[ "plattformHeight" ]
    offsetXBottomRight = (  imgWidth - bottom_right_paper_point[ 1 ] ) / imgWidth * SETTINGS[ "plattformWidth" ]
 
    return { "paperRotation": paperRotation, "bottom_left":   { "offset-Y": offsetYBottomLeft, "offset-X": offsetXBottomLeft }, 
                                              "top_left":     { "offset-Y": offsetYTopLeft, "offset-X": offsetXTopLeft },
                                              "bottom_right": { "offset-Y": offsetYBottomRight, "offset-X": offsetXBottomRight },
                                              "top_right":    { "offset-Y": offsetYTopRight, "offset-X": offsetXTopRight }  }

def removeImageParts( img1 : np.ndarray, img2 : np.ndarray ) -> np.ndarray:
    """
    Detect the paper based on the hsv values 
    Replace the parts in the image 1 where a paper in image 2 is detected
    """
    global SETTINGS

    cv2.imwrite( "./images/img1.png", img1 )
    cv2.imwrite( "./images/img2.png", img2 )
    
    img1 = np.where( img1 == 255, img1, img2 )
    img1 = np.where( img2 == 255, img2, img1 )
    return img1

def penDetection( image, loadCopy = False ):
    global SETTINGS

    if loadCopy:
        SETTINGS = json.load( open( "./config_copy.json", "r" ) )

    hsv_penImg = cv2.cvtColor( image, cv2.COLOR_BGR2HSV )

    image = markerDetection( hsv_penImg, ( SETTINGS[ "pen" ][ "h-min" ], SETTINGS[ "pen" ][ "h-max" ] ), 
                                         ( SETTINGS[ "pen" ][ "s-min" ], SETTINGS[ "pen" ][ "s-max" ] ),
                                         ( SETTINGS[ "pen" ][ "v-min" ], SETTINGS[ "pen" ][ "v-max" ] ) )

    return image

def testImage():
    img = cv2.imread( "./images/rpImg1.png" )

    img = cv2.copyMakeBorder( img, 300, 300, 300, 300, cv2.BORDER_CONSTANT )

    plattformCords = markerPlattformCoords( img )

    img = undisturbImg( img, plattformCords )

    cv2.imwrite( "./images/undisturbed1.png", img )

    coords = getCoords( img ) 

    #Transform the images to get the paper from bird view
    plattformImg = transform( img, coords[ 0 ] )

    cv2.imwrite( "./images/plattformImg1.png", plattformImg )

    stableDiffImg1 = transform( plattformImg, coords[ 1 ], device = "paper" )

    cv2.imwrite( "./images/stableDiffImg1.png", stableDiffImg1 )

    offsets = getRealWorldPaperPoints( coords, plattformImg.shape[ 1 ], plattformImg.shape[ 0 ] )
    
    #for i in range( len( coords[ 1 ] ) ):
    #    plattformImg = cv2.circle( plattformImg, ( int( coords[ 1 ][ i ][ 1 ] ), int( coords[ 1 ][ i ][ 0 ] ) ), 10, ( 0, 255, 0 ), -1 )
    
    stableDiffImg1 = transform( plattformImg, coords[ 1 ], device = "paper" )

    penImg = penDetection( stableDiffImg1 )

    plt.imshow( stableDiffImg1 )
    plt.show()
    #Convert the image to grayscale to detect where the user has drawn

def preprocessImg( img ):
    #img = cv2.rotate( img, cv2.ROTATE_90_COUNTERCLOCKWISE )
    #img = cv2.rotate( img, cv2.ROTATE_90_COUNTERCLOCKWISE )

    img = cv2.copyMakeBorder( img, 200, 200, 200, 200, cv2.BORDER_CONSTANT )
    return img

def process( img1, img2, set ):
    #prepcoess the images
    global SETTINGS
    SETTINGS = set
    img1 = preprocessImg( img1 )
    img2 = preprocessImg( img2 )

    #Detect the coordinates of the plattform and paper
    plattformCords = markerPlattformCoords( img1 )
    img1 = undisturbImg( img1, plattformCords )

    try:
        cv2.imwrite( "./images/undisturbed1.png", img1 )
    except:
        pass

    plattformCords = markerPlattformCoords( img2 )
    img2 = undisturbImg( img2, plattformCords )

    try:
        cv2.imwrite( "./images/undisturbed2.png", img2 )
    except:
        pass

    coords = getCoords( img1 ) 

    #Transform the images to get the paper from bird view
    plattformImg = transform( img1, coords[ 0 ] )
    stableDiffImg1 = transform( plattformImg, coords[ 1 ], device = "paper" )
    
    try:
        cv2.imwrite( "./images/stableDiffImg1.png", stableDiffImg1 )
    except:
        pass

    #Get the offsets of the image
    offsets = getRealWorldPaperPoints( coords, plattformImg.shape[ 1 ], plattformImg.shape[ 0 ] )

    #Transform the images to get the paper from bird view
    plattformImg = transform( img2, coords[ 0 ] )
    stableDiffImg2 = transform( plattformImg, coords[ 1 ], device = "paper" )

    try:
        cv2.imwrite( "./images/stableDiffImg2.png", stableDiffImg2 )
    except:
        pass

    #Remove the hidden servo parts

    penImg1 = penDetection( stableDiffImg1 )
    penImg2 = penDetection( stableDiffImg2 )

    mergedImg = removeImageParts( penImg1, penImg2 )
    mergedImg = mergedImg.astype( np.uint8 )

    return { "img": mergedImg, "offsets": offsets }

if __name__ == "__main__":
    SETTINGS = json.load( open( "./raspberryPi/config.json", "r" ) )
    
    testImage()

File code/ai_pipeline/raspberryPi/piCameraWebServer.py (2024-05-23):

from flask import Flask, render_template, send_file
import matplotlib.pyplot as plt
import cv2
import numpy as np
from io import BytesIO
import pdars
import flask
import time
import json

"""
Checking for existing settings and create a copy of those settings
If no settings exist create new settings
"""
try:
    SETTINGS = json.load( open( "./config.json", "r" ) )
except:
    SETTINGS = {"plattformHeight": 290, "plattformWidth": 167, "marker-height": 24.8, "marker-width": 39.8, "paperHeight": 210, "paperWidth": 148, "camera": {"brightness": 50, "sharpness": 0, "contrast": 50}, "pen": {"h-min": 0, "h-max": 255, "s-min": 0, "s-max": 255, "v-min": 55, "v-max": 150}, "markers": {"h-min": 100, "h-max": 125, "s-min": 200, "s-max": 255}, "plattform": {"h-min": 55, "h-max": 110, "s-min": 20, "s-max": 115}}


SETTINGS = json.load( open( "./config.json", "r" ) )
json.dump( SETTINGS, open( "./config_copy.json", "w+" ))


"""
Ckeck if it is possible to capture images with the raspberry pi camera
"""


from picamera2 import Picamera2
CAMERA = Picamera2()
config = CAMERA.create_preview_configuration()
CAMERA.configure(config)


CAMERA.options["quality"] = 100

CAMERA.controls.Brightness  = ( SETTINGS[ "camera" ][ "brightness" ] - 50 ) / 100
CAMERA.controls.Sharpness  = ( SETTINGS[ "camera" ][ "sharpness" ] - 50 ) / 100

CAMERA.start_preview()
CAMERA.start()
time.sleep( 0.5 )
CAMERA.capture_file( "./IMAGE.jpg" )


img = cv2.imread("./IMAGE.jpg" )
img = cv2.rotate( img, cv2.ROTATE_90_CLOCKWISE )
img = cv2.rotate( img, cv2.ROTATE_90_CLOCKWISE )
img = cv2.rotate( img, cv2.ROTATE_90_CLOCKWISE )
cv2.imwrite( "./IMAGE.jpg", img )
print( "Image shape:", img.shape )

image_path = "./IMAGE.jpg"
IMAGE = cv2.imread(image_path)
IMAGE = cv2.copyMakeBorder( IMAGE, 200, 200, 200, 200, cv2.BORDER_CONSTANT )


#Initialize the flask app
app = Flask(__name__)


@app.route('/')
def index():
    return render_template('index.html')

###
#
# Save values
#
###

@app.route( "/saveCameraValues", methods = [ "POST" ] )
def saveCameraValues():
    configSettings = json.load( open( "./config.json", "r" ) )

    data = json.loads( flask.request.data )

    configSettings[ "camera" ] = {
        "brightness": int( data[ "brightness" ] ),
        "sharpness": int( data[ "sharpness" ] ),
        "contrast": int( data[ "contrast" ] )
    }

    json.dump( configSettings, open( "./config.json", "w+" ) )

    return "200"

@app.route( "/savePaperValues", methods = [ "POST" ] )
def savePaperValues():
    configSettings = json.load( open( "./config.json", "r" ) )

    data = json.loads( flask.request.data )

    configSettings[ "plattform" ][ "h-min" ] = int( data[ "h-min" ] )
    configSettings[ "plattform" ][ "h-max" ] = int( data[ "h-max" ] )
    configSettings[ "plattform" ][ "s-min" ] = int( data[ "s-min" ] )
    configSettings[ "plattform" ][ "s-max" ] = int( data[ "s-max" ] )

    json.dump( configSettings, open( "./config.json", "w+" ) )

    return "200"

@app.route( "/saveMarkerValues", methods = [ "POST" ] )
def saveMarkerValues():
    configSettings = json.load( open( "./config.json", "r" ) )

    data = json.loads( flask.request.data )

    configSettings[ "markers" ][ "h-min" ] = int( data[ "h-min" ] )
    configSettings[ "markers" ][ "h-max" ] = int( data[ "h-max" ] )
    configSettings[ "markers" ][ "s-min" ] = int( data[ "s-min" ] )
    configSettings[ "markers" ][ "s-max" ] = int( data[ "s-max" ] )

    json.dump( configSettings, open( "./config.json", "w+" ) )

    return "200"

@app.route( "/savePenValues", methods = [ "POST" ] )
def savePenValues():
    configSettings = json.load( open( "./config.json", "r" ) )

    data = json.loads( flask.request.data )

    configSettings[ "pen" ][ "h-min" ] = int( data[ "h-min" ] )
    configSettings[ "pen" ][ "h-max" ] = int( data[ "h-max" ] )
    configSettings[ "pen" ][ "s-min" ] = int( data[ "s-min" ] )
    configSettings[ "pen" ][ "s-max" ] = int( data[ "s-max" ] )
    configSettings[ "pen" ][ "v-min" ] = int( data[ "v-min" ] )
    configSettings[ "pen" ][ "v-max" ] = int( data[ "v-max" ] )

    json.dump( configSettings, open( "./config.json", "w+" ) )

    return "200"


@app.route( "/savePenSize", methods = [ "POST" ] )
def savePenSize():
    configSettings = json.load( open( "./config.json", "r" ) )

    data = json.loads( flask.request.data )

    configSettings[ "penSize" ] = int( data[ "value" ] )

    json.dump( configSettings, open( "./config.json", "w+" ) )

    return "200"


###
#
# Send the images
#
###
@app.route( "/take_image", methods = [ "POST" ],  )
def take_image():
    global IMAGE, CAMERA

    data = json.loads( flask.request.data )

    SETTINGS[ "camera" ][ "brightness" ] = int( data[ "brightness" ] )
    SETTINGS[ "camera" ][ "sharpness" ] = int( data[ "sharpness" ] )
    SETTINGS[ "camera" ][ "contrast" ] = int( data[ "contrast" ] )
    json.dump( SETTINGS, open( "./config_copy.json", "w+" ))
    
    CAMERA.controls.Brightness  = ( float( data[ "brightness" ] ) - 50 ) / 100
    CAMERA.controls.Sharpness  = ( float( data[ "sharpness" ] ) - 50 ) / 100

    CAMERA.capture_file( "./IMAGE.jpg" )

    img = cv2.imread("./IMAGE.jpg" )
    img = cv2.rotate( img, cv2.ROTATE_90_CLOCKWISE )
    img = cv2.rotate( img, cv2.ROTATE_90_CLOCKWISE )
    img = cv2.rotate( img, cv2.ROTATE_90_CLOCKWISE )
    cv2.imwrite( "./IMAGE.jpg", img )

    print( "Image shape:", img.shape )

    IMAGE = cv2.imread( "./IMAGE.jpg" )
    IMAGE = cv2.copyMakeBorder( IMAGE, 200, 200, 200, 200, cv2.BORDER_CONSTANT )

    return "200"

@app.route('/markerHSV', methods = [ "POST" ] ) 
def markerHSV():
    data = json.loads( flask.request.data )

    SETTINGS[ "markers" ][ "h-min" ] = int( data[ "h-min" ] )
    SETTINGS[ "markers" ][ "h-max" ] = int( data[ "h-max" ] )
    SETTINGS[ "markers" ][ "s-min" ] = int( data[ "s-min" ] )
    SETTINGS[ "markers" ][ "s-max" ] = int( data[ "s-max" ] )

    json.dump( SETTINGS, open( "./config_copy.json", "w+" ))
    
    return "200"

@app.route('/paperHSV', methods = [ "POST" ] ) 
def paperHSV():
    data = json.loads( flask.request.data )

    SETTINGS[ "plattform" ][ "h-min" ] = int( data[ "h-min" ] )
    SETTINGS[ "plattform" ][ "h-max" ] = int( data[ "h-max" ] )
    SETTINGS[ "plattform" ][ "s-min" ] = int( data[ "s-min" ] )
    SETTINGS[ "plattform" ][ "s-max" ] = int( data[ "s-max" ] )

    json.dump( SETTINGS, open( "./config_copy.json", "w+" ))
    
    return "200"

@app.route('/penHSV', methods = [ "POST" ] ) 
def penHSV():
    data = json.loads( flask.request.data )

    SETTINGS[ "pen" ][ "h-min" ] = int( data[ "h-min" ] )
    SETTINGS[ "pen" ][ "h-max" ] = int( data[ "h-max" ] )
    SETTINGS[ "pen" ][ "s-min" ] = int( data[ "s-min" ] )
    SETTINGS[ "pen" ][ "s-max" ] = int( data[ "s-max" ] )
    SETTINGS[ "pen" ][ "v-min" ] = int( data[ "v-min" ] )
    SETTINGS[ "pen" ][ "v-max" ] = int( data[ "v-max" ] )

    json.dump( SETTINGS, open( "./config_copy.json", "w+" ))
    
    return "200"
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

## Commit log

2023-03-31 crated project
    [simple_connector_mk2.kicad_pcb, simple_connector_mk2.kicad_sch]
2023-04-11 created projects
    [drake_electronics.kicad_pcb, drake_electronics.kicad_sch]
2023-04-12 deleted backups
    [drake_electronics.kicad_sch]
2023-04-12 basic schematic
    [drake_electronics.kicad_sch]
2023-04-13 finsihed basic electronics
    [drake_electronics.kicad_sch]
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2023-04-14 updated workhours
    [Workhours.xlsx]
2023-06-13 new partslist
    [Partslist.xlsx]
2023-06-20 delete repository
    deleting because of a github desktop error
    [drake_electronics.kicad_pcb, drake_electronics.kicad_sch]
2023-06-20 version 2 of cad
    [A_head.cfg, A_head_ground.cfg, A_middle_axis_lifter_asm_left.cfg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]
2023-07-22 linear achses changed
    the x and y achses has been changed from a trapezoidal spindle spindeln driver to a toothed belt drive
    [A_head.cfg, A_head_ground.cfg, A_middle_axis_lifter_asm_left.cfg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]
2023-07-28 Update licenses
    [Partslist.xlsx, Workhours.xlsx]
2023-08-29 Improved Covering
    [A_frame_cover_back.cfg, A_frame_endswitch_holder.cfg, A_head.cfg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]
2023-08-29 Octagon improved
    Changed the side parts of the octagon so that front and back is the same.
    [A_octagon_back.cfg, A_octagon_front.cfg, A_side_axis_stepper_connector.cfg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]
2023-08-30 New construction
    [A_frame_cover_back.cfg, A_frame_endswitch_holder.cfg, A_head.cfg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]
2023-09-01 first finished version
    everything should work.
    To-Do:
    Head
    Hand with camera
    Touchpannel
    [1_glas_bottom.psm, 1_octagone_back_top_cover.psm, 1_octagone_front_top_cover.psm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]
2023-09-01 no welding needed anymore
    [a1_DrAi.cfg, a1_frame_base_left.cfg, a1_head.cfg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]
2023-09-01 Feet and arms
    [a1_DrAi.cfg, a1_arm.cfg, a1_arm_left.cfg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]
2023-09-10 2d Construction and paper Holding
    [1_glas_bottom.psm, 1_octagone_back_top_cover.psm, 1_octagone_front_top_cover.psm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]
2023-09-11 New Paper holding design
    [1_glas_bottom.psm, a1_DrAi.cfg, a1_paper.cfg]
2023-09-20 New Base
    Manufacturing of the base is now better, bevor we used screws now we use weilding
    [1_glas_bottom.psm, 1_octagone_back_top_cover.psm, 1_octagone_front_top_cover.psm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]
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2023-09-20 updates with printer files
    [1_side_axis_stepper.stl]
2023-09-21 Divided Stepper Connector into 3 parts
    [1_octagone_back_top_cover.psm, 1_octagone_front_top_cover.psm, N2_Jaw_Coupling_5xTr8.cfg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]
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2023-10-01 final cover without screws
    [a1_DrAi.cfg, a1_arm.cfg, a1_arm_left.cfg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]
2023-10-01 sliced first printer files
    [1_side_axis_stepper.stl, 2_side_axis_stepper_right.stl, 3_side_axis_stepper_left.stl]
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2023-10-02 Hole distance of H8-Lager changed
    [A_pen_asm.cfg, a1_paper.cfg, a_drake.cfg]
2023-10-02 merging branches for current cad status
    [1_glas_bottom.psm, 1_octagone_back_top_cover.psm, 1_octagone_front_top_cover.psm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]
2023-10-02 new printer files (sideaxis)
    [1_side_axis_end_switch_holder_long.stl, 1_side_axis_stepper.stl]
2023-10-02 added "side axis end switch" printer files
    [2_side_axis_end_switch_holder.stl]
2023-10-02 added "side axis spindle bearing" printer files
    [3_side_axis_trapezoidal_spindle_bearing.stl]
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2023-10-11 stabilized rework
    [2_feet_side.stl, a5_head.cfg, a6a_arm_left.cfg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]
2023-10-16 2d construction
    2d construction for the aluminium parts created. just the dft-files no pdf-files. time = 14h
    holes of aluminium parts changed to a wider diameter. d5 is now d6 for example
    [1a_octagone_front_top_cover.psm, 1b_octagone_back_top_cover.psm, a1.1_frame_base.cfg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]
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2023-12-11 Revert "Sync"
    This reverts commit bab961ebb3a3366b939c12edf7ff7a805feb5cd6.
    [1_feet_front.stl, 1_glas_bottom.psm, 1_octagone_back_top_cover.psm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]
2023-12-11 moved x-achsis in z-direction
    because of manufacturing simplicity a cut in the u-profiles was not manufactured. because of that reason the x-achsis has to be moved 5 milimiters in the positiv z-direction
    [a1.1_frame_base.cfg, a1.2.1b_octogon_segment_mirror.cfg, a1.2a_octagon_back.cfg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]
2023-12-13 pen_holder_updated
    the old penholder uses feathers to hold the pen. the new one uses screws
    [a7_pen.cfg, a_drake.cfg, a_drake_without_cover.cfg]
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2023-12-21 octagon floor improvisation
    the octagon couldn't be manufactored in time. due to this reason the octagon floor will be 3d printed
    [a1_frame.cfg, a3.1_side_axis_stepper_connector.cfg, a7_pen.cfg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]
2023-12-30 paper holder markers
    to better identify the platform, special markers are added to the platform
    [a4_paper.cfg, a_drake.cfg, a_drake_without_cover.cfg]
2023-12-31 updated left arm
    the camera couldn't capture the hole image and for that reason the camera position has been moved to a higher position and a different angle
    [a4_paper.cfg, a6a_arm_left.cfg, a_drake.cfg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]
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2024-02-11 updated left arm
    to get a better view on the paper the arm has been updated with connectors to make him more flexible
    [a6.a1_arm_left.cfg, a_drake.cfg]
2024-03-17 Better documentation and scripts
    [a_drake.cfg]
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2024-03-19 new files and graphs
    [e1_dm422t.step, e2_lrs-350-24.step]
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2024-04-08 updated mountingplate
    to cover the issues of the mounting plate extrensions for the stop sensor trigger are improved
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2024-04-25 fixed bugs of the ai
    [diff1_history.txt]
2024-05-08 camera webserver bug fixing
    [pdars.py, piCameraWebServer.py, rpWebServer.py]
2024-05-15 bugs fixed
    [diff1_history.txt]
2024-05-15 fixed gpu support bug
    [layers.py]
2024-05-23 test server for better visualization of the ai
    to better display the process of the ai a webserver has been programmed for the user. with that webserver the user is able to see the drawing process and in addition can edit images direct in the bro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
    [diff1_history.txt]
